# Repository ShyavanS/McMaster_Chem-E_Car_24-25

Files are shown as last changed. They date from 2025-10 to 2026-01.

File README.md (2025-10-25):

# McMaster_Chem-E_Car_24-25
The codebase for the McMaster Chem-E Car Team from 2024-2025.

This project uses an Adafruit Feather RP2040 Adalogger microcontroller programmed in the Arduino programming language. The car runs off a chemical reaction and is stopped by a chemical reaction as well. However, the code and the microcontroller are used to start the stopping reaction and stir the mixtures while monitoring it to identify when to stop based on a temperature threshold. It also uses an IMU to keep the car going straight, a servo for starting the stopping reaction, two motor drivers to run the drive motors, and two motors for stirring the reactions. The car's main drive system will be powered from a custom-built alkaline battery while the remaining auxiliary systems are powered from a smaller Li-Po battery.

The major components used are as follows:<br />
2 - N20 100 RPM Motors (for drive system)<br />
2 - N20 1000 RPM Motor (for reaction stirring mechanisms)<br />
4 - SER0039 Servo Motor (for initially mixing reactants & steering)<br />
2 - DRV8847 Motor Drivers (only used as switches as per regulations)<br />
2 - AMT102 Rotary Encoders (for datalogging to tune braking model only)<br />
1 - DS18B20 Temperature Sensor (for measuring temperature of braking reaction)<br />
1 - Adafruit 9-DOF Orientation IMU Fusion Breakout (BNO085 for logging/maintaining heading)<br /> 
1 - Adafruit Feather RP2040 Adalogger Microcontroller<br />
1 - 5000 mAh Li-Po Battery<br />

This repository also contains the custom-made PCB design for the component wiring we are using this year. The design was made using Altium, source files & gerber files are present in this repository.

The main objective of the competition is to design a small car to carry a certain amount of weight a set distance while powering and stopping the vehicle with a chemical reaction. The distance and weight vary each year. The compectition is hosted by the American Institute of Chemical Engineers (AIChE).

Makes use of [pimoroni's encoder-pio driver](https://github.com/pimoroni/pimoroni-pico/tree/encoder-pio/drivers/encoder-pio) to count encoder ticks on the PIOs of the RP2040 to prefvent lost ticks due to higher priority interrupts and increase accuracy while decreasing CPU load. Minor modifications were made to remove debouncing functionality & delays.

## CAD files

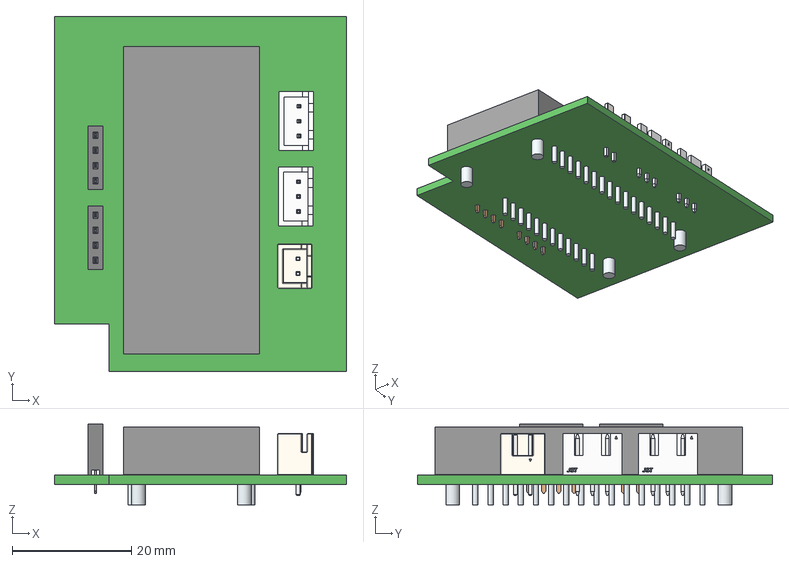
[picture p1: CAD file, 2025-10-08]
Car_Circuitry/Steering_Daughterboard.step
49.0 x 59.6 x 13.5 mm
Leads x 32
Pins x 2
Marking x 2
JST Logo x 2
B2B-XH-A
JST Logo adjustable
6130xx11821_PIN x 8

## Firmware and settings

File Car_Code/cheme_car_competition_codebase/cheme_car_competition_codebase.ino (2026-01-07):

// McMaster Chem-E Car Team
// Chem-E Car Competition Code - 24/25

/*
The code to be used at the Chem-E Car competition to run the car. Makes use of
an RP2040 microcontroller to drive the car and stop at a specified distance.
More information is available in the readme.
*/

// Included libraries
#include <OneWire.h>
#include <Adafruit_BNO08x.h>
#include <DallasTemperature.h>
#include <Servo.h>
#include <Adafruit_NeoPixel.h>
#include "hardware/timer.h"

#define NUM_LEDS 1 // Status LED

// Define drive motor pins
#define LEFT_PWM_1 9
#define LEFT_PWM_2 10
#define RIGHT_PWM_1 12
#define RIGHT_PWM_2 11

// Define the PWM pins for the stir bar motors
#define BRAK_STIR_PWM_1 A3
#define BRAK_STIR_PWM_2 24
#define PROP_STIR_PWM_1 6
#define PROP_STIR_PWM_2 5

// Define servo pins
#define BRAK_SERVO_PWM 13
#define PROP_SERVO_PWM 4
#define LEFT_SERVO_PWM MOSI
#define RIGHT_SERVO_PWM SCK

#define BRAK_TEMP_SENS A1 // Pin for the teperature sensor data line

#define BNO08X_RESET -1 // No reset pin for IMU over I2C, only enabled for SPI

// Struct for Euler Angles
struct euler_t
{
  float yaw;
  float pitch;
  float roll;
} ypr;

// Create servo objects
Servo brak_servo;
Servo prop_servo;
Servo left_servo;
Servo right_servo;

// Create BNO085 instance
Adafruit_BNO08x bno08x(BNO08X_RESET);
sh2_SensorValue_t sensor_value;

OneWire one_wire(BRAK_TEMP_SENS);          // Create a OneWire instance to communicate with the sensor
DallasTemperature temp_sensors(&one_wire); // Pass OneWire reference to Dallas Temperature sensor

Adafruit_NeoPixel pixel(NUM_LEDS, PIN_NEOPIXEL, NEO_GRB + NEO_KHZ800); // Status LED

// The target yaw angle to keep car straight
const float GOAL_YAW = 0.0;

// Rejection threshold for noise in IMU measurements
const float REJECT_THRESHOLD = 3.0;

// Define IMU variables
double raw_yaw;        // raw yaw angle
double prev_yaw;       // previous unwrapped yaw angle
double yaw;            // unwrapped yaw angle
double init_yaw = 0.0; // initial yaw angle
double yaw_diff = 0.0; // yaw angle difference

// Delta temperature
double temp_diff;

// Temperature change threshold
double temp_change;

// Last temperature fetched flag
bool last_fetch;

// variables to store temperature
double temperature_c; // Current temperature
double init_temp;     // Initial temperature for differential calculation

// KALMAN FILTER variables
double x_temp; // Filtered temperature
double p_temp; // Initial error covariance
double x_imu;  // Filtered temperature
double p_imu;  // Initial error covariance

// Process noise and measurement noise
double q_temp; // Process noise covariance
double r_temp; // Measurement noise covariance
double q_imu;  // Process noise covariance
double r_imu;  // Measurement noise covariance

// Keeping track of time
double curr_time = 0.0f;
double prev_time = 0.0f;
uint32_t start_time;

// PID loop variables
double error = 0.0;      // Proportional error
double last_error = 0.0; // Derivative error
double sum_error = 0.0;  // Integral error

// The following numbers need to be adjusted through testing
const float K_P = 13.0; // Proportional weighting
const float K_I = 0.0;  // Integral weighting
const float K_D = 0.0;  // Derivative weighting

// Offsets & constants for PID
int left_offset = 0;
int right_offset = 0;
const int SERVO_ANGLE = 1475;
const int MAX_OFFSET = 1024;
const int YAW_REF = 90;

/*
Description: Subroutine to drive car forward.
Inputs:      void
Outputs:     void
Parameters:  void
Returns:     void
*/
void drive_forward(void)
{
  digitalWrite(LEFT_PWM_1, HIGH);
  digitalWrite(RIGHT_PWM_2, HIGH);
  digitalWrite(LEFT_PWM_2, LOW);
  digitalWrite(RIGHT_PWM_1, LOW);
}

/*
Description: Subroutine to stop car and brake motors.
Inputs:      void
Outputs:     void
Parameters:  void
Returns:     void
*/
void stop_driving(void)
{
  digitalWrite(LEFT_PWM_1, HIGH);
  digitalWrite(RIGHT_PWM_2, HIGH);
  digitalWrite(LEFT_PWM_2, HIGH);
  digitalWrite(RIGHT_PWM_1, HIGH);
}

/*
Description: Subroutine to dump reactants into vessel.
Inputs:      void
Outputs:     void
Parameters:  (Servo)servo, (int)angle_us, (int)delay_ms
Returns:     void
*/
void servo_dump(Servo servo, int angle_us, int delay_ms)
{
  // Rotate to specified position
  servo.writeMicroseconds(angle_us);
  busy_wait_ms(500);
  servo.writeMicroseconds(angle_us);

  busy_wait_ms(delay_ms); // Wait specified delay

  // Return to default position
  servo.writeMicroseconds(450);
  busy_wait_ms(500);
  servo.writeMicroseconds(450);
}

/*
Description: Subroutine to set speed for reaction stir motors.
Inputs:      void
Outputs:     void
Parameters:  (int)stir_pin_1, (int)stir_pin_2, (int)speed
Returns:     void
*/
void start_stir(int stir_pin_1, int stir_pin_2, int speed) // Start stirring mechanism
{
  digitalWrite(stir_pin_1, LOW);  // For fast decay
  analogWrite(stir_pin_2, speed); // Set motor to speed obtained through testing
}

/*
Description: Subroutine to implement Kalman filtering on temperature sensor data.
Inputs:      void
Outputs:     (double)x_temp, (double)p_temp
Parameters:  (double)x_k, (double)p_k, (double)q, (double)r, (double)input
Returns:     void
*/
void kalman_filter(double x_k, double p_k, double q, double r, double input, bool tempTrue)
{
  // Kalman filter prediction
  double x_k_minus = x_k;     // Predicted next state estimate
  double p_k_minus = p_k + q; // Predicted error covariance for the next state

  // Kalman filter update

  /* Kalman gain: calculated based on the predicted error covariance
  and the measurement noise covariance, used to update the
  state estimate (x_k) and error covariance (p_k) */
  double k = p_k_minus / (p_k_minus + r); // Kalman gain

  // Comparison with actual sensor reading
  x_k = x_k_minus + k * (input - x_k_minus); // Updated state estimate
  p_k = (1 - k) * p_k_minus;                 // Updated error covariance

  if (tempTrue) // Update state for temperature sensor or IMU accordingly
  {
    x_temp = x_k;
    p_temp = p_k;
  }
  else
  {
    x_imu = x_k;
    p_imu = p_k;
  }
}

/*
Description: Subroutine to set the desired reports on the IMU.
Inputs:      void
Outputs:     void
Parameters:  void
Returns:     void
*/
void set_reports(void)
{
  if (!bno08x.enableReport(SH2_ROTATION_VECTOR))
  {
    exit(0);
  }
}

/*
Description: Subroutine convert quaternions from the IMU into euler angles to obtain yaw.
Inputs:      void
Outputs:     void
Parameters:  (float)qr, (float)qi, (float)qj, (float)qk, (euler_t)*ypr, (bool)degrees
Returns:     void
*/
void quaternion_to_euler(float qr, float qi, float qj, float qk, euler_t *ypr, bool degrees = false)
{
  float sqr = sq(qr);
  float sqi = sq(qi);
  float sqj = sq(qj);
  float sqk = sq(qk);

  ypr->yaw = atan2(2.0 * (qi * qj + qk * qr), (sqi - sqj - sqk + sqr));
  ypr->pitch = asin(-2.0 * (qi * qk - qj * qr) / (sqi + sqj + sqk + sqr));
  ypr->roll = atan2(2.0 * (qj * qk + qi * qr), (-sqi - sqj + sqk + sqr));

  if (degrees)
  {
    ypr->yaw *= RAD_TO_DEG;
    ypr->pitch *= RAD_TO_DEG;
    ypr->roll *= RAD_TO_DEG;
  }
}

/*
Description: Pointer subroutine for euler angles.
Inputs:      void
Outputs:     void
Parameters:  (sh2_RotationVectorWAcc_t)*rotational_vector, (float)qi, (euler_t)*ypr, (bool)degrees
Returns:     void
*/
void quaternion_to_euler_RV(sh2_RotationVectorWAcc_t *rotational_vector, euler_t *ypr, bool degrees = false)
{
  quaternion_to_euler(rotational_vector->real, rotational_vector->i, rotational_vector->j, rotational_vector->k, ypr, degrees);
}

/*
Description: PID loop subroutine to adjust steering angle.
Inputs:      (double)error, (double)sum_error, (double)last_error, (double)curr_time, (double)prev_time
Outputs:     (int)adj_pid_output
Parameters:  void
Returns:     void
*/
void pid_loop(void)
{
  // Generate output of controller based on constants & errors
  double pid_output = (error * K_P + sum_error * K_I + (error - last_error) / (curr_time - prev_time) * K_D) / YAW_REF * MAX_OFFSET;
  int adj_pid_output = max(min(round(pid_output), MAX_OFFSET), -MAX_OFFSET); // Clamp output to bounds

  // Get IMU reading to update error values
  bno08x.getSensorEvent(&sensor_value);
  quaternion_to_euler_RV(&sensor_value.un.rotationVector, &ypr, true);

  // Process yaw angle
  raw_yaw = ypr.yaw;
  unwrap_yaw();
  yaw_diff = yaw - init_yaw;

  kalman_filter(x_imu, p_imu, q_imu, r_imu, yaw_diff, false); // Kalman filtering for IMU data

  // Update errors
  last_error = error;
  error = GOAL_YAW - x_imu;
  sum_error = max(min(sum_error + cbrt(error), MAX_OFFSET), -MAX_OFFSET);

  // Write to servos
  left_servo.writeMicroseconds(SERVO_ANGLE - adj_pid_output);
  right_servo.writeMicroseconds(SERVO_ANGLE - adj_pid_output);
}

/*
Description: Subroutine to fetch temperature form the temperature sensor when the data is ready.
Inputs:      void
Outputs:     (double)temperature_c
Parameters:  void
Returns:     void
*/
void fetch_temp(void)
{
  temperature_c = temp_sensors.getTempCByIndex(0); // Get temperature in Celsius

  // Update temperature kalman filter
  kalman_filter(x_temp, p_temp, q_temp, r_temp, temperature_c, true);

  temp_diff = x_temp - init_temp; // Update delta temperature
  last_fetch = true;              // Raise fetch flag to signal ready
}

/*
Description: Subroutine to unwrap yaw angle to prevent discontinuities in the function over time.
Inputs:      (double)raw_yaw, (double)prev_yaw
Outputs:     (double)yaw
Parameters:  void
Returns:     void
*/
void unwrap_yaw(void)
{
  double delta = raw_yaw - prev_yaw;

  delta = fmod(delta + 180.0, 360.0);

  if (delta < 0.0)
  {
    delta += 360.0;
  }

  delta -= 180.0;

  // Reject any sudden noisy spikes
  if (fabs(delta) > REJECT_THRESHOLD)
  {
    yaw = prev_yaw;
    prev_yaw = yaw;
  }
  else
  {
    yaw = prev_yaw + delta;
    prev_yaw = yaw;
  }
}

/*
Description: Arduino setup subroutine.
Inputs:      void
Outputs:     void
Parameters:  void
Returns:     void
*/
void setup(void)
{
  // Indicate status to be initialized
  pixel.begin();
  pixel.setBrightness(255);
  pixel.show();
  pixel.setPixelColor(0, 255, 0, 0);
  pixel.show();

  // Setting to drive motors output mode
  pinMode(LEFT_PWM_1, OUTPUT);
  pinMode(LEFT_PWM_2, OUTPUT);
  pinMode(RIGHT_PWM_1, OUTPUT);
  pinMode(RIGHT_PWM_2, OUTPUT);

  stop_driving(); // Stop driving motors from any residual bootloader code

  // Initialize the stir motor pins as outputs
  pinMode(BRAK_STIR_PWM_1, OUTPUT);
  pinMode(BRAK_STIR_PWM_2, OUTPUT);
  pinMode(PROP_STIR_PWM_1, OUTPUT);
  pinMode(PROP_STIR_PWM_2, OUTPUT);

  // Setting the stir speed
  start_stir(BRAK_STIR_PWM_1, BRAK_STIR_PWM_2, 255);
  start_stir(PROP_STIR_PWM_1, PROP_STIR_PWM_2, 255);

  temp_sensors.begin();                     // Initialize the DS18B20 sensor
  temp_sensors.setResolution(11);           // Reduce resolution for faster polling
  temp_sensors.requestTemperatures();       // Request temperature from all devices on the bus
  temp_sensors.setWaitForConversion(false); // Disable blocking to allow multitasking

  init_temp = temp_sensors.getTempCByIndex(0); // Get temperature in Celsius
  temperature_c = init_temp;                   // Initialize temperature variable
  last_fetch = true;                           // Raise fetch flag to signal ready
  temp_diff = 0.0;                             // Initialize delta temperature to zero

  bno08x.begin_I2C();
  set_reports();

  // Poll IMU a few times & wait for initialization value to stabilize
  for (int i = 0; i < 5; i++)
  {
    bno08x.getSensorEvent(&sensor_value);
    quaternion_to_euler_RV(&sensor_value.un.rotationVector, &ypr, true);

    init_yaw = ypr.yaw;
    raw_yaw = init_yaw;
    prev_yaw = init_yaw;
    yaw = init_yaw;
    yaw_diff = yaw - init_yaw;

    busy_wait_ms(200);
  }

  // Initialize Kalman filter parameters
  x_temp = init_temp; // Initial state estimate
  p_temp = 0.1;       // Initial error covariance
  q_temp = 0.01;      // Process noise covariance
  r_temp = 0.5;       // Measurement noise covariance
  x_imu = yaw_diff;   // Initial state estimate
  p_imu = 0.007;      // Initial error covariance
  q_imu = 0.005;      // Process noise covariance
  r_imu = 0.01;       // Measurement noise covariance

  // Initialize servos to default position
  prop_servo.writeMicroseconds(450);
  prop_servo.attach(PROP_SERVO_PWM, 400, 2600);
  prop_servo.writeMicroseconds(450);
  busy_wait_ms(2000);
  brak_servo.writeMicroseconds(450);
  brak_servo.attach(BRAK_SERVO_PWM, 400, 2600);
  brak_servo.writeMicroseconds(450);
  busy_wait_ms(2000);
  left_servo.writeMicroseconds(1475);
  left_servo.attach(LEFT_SERVO_PWM, 400, 2600);
  left_servo.writeMicroseconds(1475);
  busy_wait_ms(2000);
  right_servo.writeMicroseconds(1475);
  right_servo.attach(RIGHT_SERVO_PWM, 400, 2600);
  right_servo.writeMicroseconds(1475);
  busy_wait_ms(2000);

  // Dump reactants before starting drive
  servo_dump(prop_servo, 2500, 3000);
  busy_wait_ms(7000);
  servo_dump(brak_servo, 2500, 3000);

  start_time = micros(); // First measurement saved seperately

  busy_wait_ms(17000);

  // Poll IMU one last time
  bno08x.getSensorEvent(&sensor_value);
  quaternion_to_euler_RV(&sensor_value.un.rotationVector, &ypr, true);

  init_yaw = ypr.yaw;
  raw_yaw = init_yaw;
  prev_yaw = init_yaw;
  yaw = init_yaw;
  yaw_diff = yaw - init_yaw;

  curr_time = (time_us_32() - start_time) / 1000000.0f; // Taken to update prev_time

  pixel.setPixelColor(0, 0, 0, 255); // Indicate setup complete status
  pixel.show();
}

/*
Description: Arduino loop subroutine.
Inputs:      void
Outputs:     void
Parameters:  void
Returns:     void
*/
void loop(void)
{
  drive_forward(); // Start drive

  prev_time = curr_time;

  // Only poll if flag indicates ready state
  if (last_fetch)
  {
    temp_sensors.requestTemperatures(); // Request temperature from all devices on the bus

    last_fetch = false; // System is no longer ready, lower flag
  }
  else if (temp_sensors.isConversionComplete())
  {
    fetch_temp(); // Fetch temperature after conversion, otherwise continue loop
  }

  curr_time = (time_us_32() - start_time) / 1000000.0f; // Taken to check time against first measurement

  pid_loop(); // Run PID controller

  temp_change = 0.185f * curr_time - 4.5f; // Calculate temperature change

  if (temp_diff <= temp_change)
  {
    // Stop driving
    stop_driving();

    // Indicate status to be finished
    pixel.setPixelColor(0, 0, 255, 0);
    pixel.show();

    while (1)
      ; // Do nothing for remainder of uptime
  }
}

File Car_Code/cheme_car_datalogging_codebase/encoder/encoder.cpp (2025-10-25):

#include <math.h>
#include <float.h>
#include "hardware/irq.h"
#include "hardware/clocks.h"
#include "encoder.hpp"

#ifndef NO_QSTR
#include "encoder.pio.h"
#endif

#define LAST_STATE(state) ((state) & 0b0011)
#define CURR_STATE(state) (((state) & 0b1100) >> 2)

namespace encoder
{

  ////////////////////////////////////////////////////////////////////////////////////////////////////
  // STATICS
  ////////////////////////////////////////////////////////////////////////////////////////////////////
  Encoder *Encoder::encoders[][NUM_PIO_STATE_MACHINES] = {{nullptr, nullptr, nullptr, nullptr}, {nullptr, nullptr, nullptr, nullptr}};
  uint8_t Encoder::claimed_sms[] = {0x0, 0x0};
  uint Encoder::pio_program_offset[] = {0, 0};

  Encoder::Capture::Capture()
      : captured_count(0), captured_delta(0), captured_frequency(0.0f), counts_per_rev(INT32_MAX)
  {
  }

  Encoder::Capture::Capture(int32_t count, int32_t delta, float frequency, float counts_per_rev)
      : captured_count(count), captured_delta(delta), captured_frequency(frequency), counts_per_rev(MAX(counts_per_rev, FLT_EPSILON))
  { // Clamp counts_per_rev to avoid potential NaN
  }

  int32_t Encoder::Capture::count() const
  {
    return captured_count;
  }

  int32_t Encoder::Capture::delta() const
  {
    return captured_delta;
  }

  float Encoder::Capture::frequency() const
  {
    return captured_frequency;
  }

  float Encoder::Capture::revolutions() const
  {
    return (float)captured_count / counts_per_rev;
  }

  float Encoder::Capture::degrees() const
  {
    return revolutions() * 360.0f;
  }

  float Encoder::Capture::radians() const
  {
    return revolutions() * M_TWOPI;
  }

  float Encoder::Capture::revolutions_delta() const
  {
    return (float)captured_delta / counts_per_rev;
  }

  float Encoder::Capture::degrees_delta() const
  {
    return revolutions_delta() * 360.0f;
  }

  float Encoder::Capture::radians_delta() const
  {
    return revolutions_delta() * M_TWOPI;
  }

  float Encoder::Capture::revolutions_per_second() const
  {
    return captured_frequency / counts_per_rev;
  }

  float Encoder::Capture::revolutions_per_minute() const
  {
    return revolutions_per_second() * 60.0f;
  }

  float Encoder::Capture::degrees_per_second() const
  {
    return revolutions_per_second() * 360.0f;
  }

  float Encoder::Capture::radians_per_second() const
  {
    return revolutions_per_second() * M_TWOPI;
  }

  Encoder::Encoder(PIO pio, uint sm, const pin_pair &pins, uint common_pin, Direction direction,
                   float counts_per_rev, bool count_microsteps, uint16_t freq_divider)
      : pio(pio), sm(sm), enc_pins(pins), enc_common_pin(common_pin), enc_direction(direction), enc_counts_per_rev(MAX(counts_per_rev, FLT_EPSILON)), count_microsteps(count_microsteps), freq_divider(freq_divider), clocks_per_time((float)(clock_get_hz(clk_sys) / (ENC_LOOP_CYCLES * freq_divider)))
  {
  }

  Encoder::~Encoder()
  {
    if (initialised)
    {
      pio_sm_set_enabled(pio, sm, false);
      pio_sm_unclaim(pio, sm);

      uint pio_idx = pio_get_index(pio);
      encoders[pio_idx][sm] = nullptr;
      claimed_sms[pio_idx] &= ~(1u << sm);

      hw_clear_bits(&pio->inte1, PIO_IRQ1_INTE_SM0_RXNEMPTY_BITS << sm);

      // If there are no more SMs using the encoder program, then we can remove it from the PIO
      if (claimed_sms[pio_idx] == 0)
      {
        pio_remove_program(pio, &encoder_program, pio_program_offset[pio_idx]);

        if (pio_idx == 0)
        {
          irq_remove_handler(PIO0_IRQ_1, pio0_interrupt_handler);
        }
        else
        {
          irq_remove_handler(PIO1_IRQ_1, pio1_interrupt_handler);
        }
      }

      // Reset all the pins this PWM will control back to an unused state
      gpio_set_function(enc_pins.a, GPIO_FUNC_NULL);
      gpio_set_function(enc_pins.b, GPIO_FUNC_NULL);

      if (enc_common_pin != PIN_UNUSED)
      {
        gpio_set_function(enc_common_pin, GPIO_FUNC_NULL);
      }
    }
  }

  void Encoder::pio_interrupt_handler(uint pio_idx)
  {
    // Go through each SM on the PIO to see which triggered this interrupt,
    // and if there's an associated encoder, have it update its state
    for (uint8_t sm = 0; sm < NUM_PIO_STATE_MACHINES; sm++)
    {
      if (encoders[pio_idx][sm] != nullptr)
      {
        encoders[pio_idx][sm]->process_steps();
      }
    }
  }

  void Encoder::pio0_interrupt_handler()
  {
    pio_interrupt_handler(0);
  }

  void Encoder::pio1_interrupt_handler()
  {
    pio_interrupt_handler(1);
  }

  bool Encoder::init()
  {
    if (!initialised && !pio_sm_is_claimed(pio, sm))
    {
      // Are the pins we want to use actually valid?
      if ((enc_pins.a < NUM_BANK0_GPIOS) && (enc_pins.b < NUM_BANK0_GPIOS))
      {

        // If a Pin C was defined, and valid, set it as a GND to pull the other two pins down
        if ((enc_common_pin != PIN_UNUSED) && (enc_common_pin < NUM_BANK0_GPIOS))
        {
          gpio_init(enc_common_pin);
          gpio_set_dir(enc_common_pin, GPIO_OUT);
          gpio_put(enc_common_pin, false);
        }

        pio_sm_claim(pio, sm);
        uint pio_idx = pio_get_index(pio);

        // If this is the first time using an encoder on this PIO, add the program to the PIO memory
        if (claimed_sms[pio_idx] == 0)
        {
          pio_program_offset[pio_idx] = pio_add_program(pio, &encoder_program);
        }

        // Initialise the A and B pins of this encoder
        pio_gpio_init(pio, enc_pins.a);
        pio_gpio_init(pio, enc_pins.b);
        gpio_pull_up(enc_pins.a);
        gpio_pull_up(enc_pins.b);

        // Set their default direction
        pio_sm_set_consecutive_pindirs(pio, sm, enc_pins.a, 1, false);
        pio_sm_set_consecutive_pindirs(pio, sm, enc_pins.b, 1, false);

        pio_sm_config c = encoder_program_get_default_config(pio_program_offset[pio_idx]);
        sm_config_set_jmp_pin(&c, enc_pins.a);
        sm_config_set_in_pins(&c, enc_pins.b);

        sm_config_set_in_shift(&c, false, false, 1);
        sm_config_set_fifo_join(&c, PIO_FIFO_JOIN_RX);

        sm_config_set_clkdiv_int_frac(&c, freq_divider, 0);

        pio_sm_init(pio, sm, pio_program_offset[pio_idx], &c);

        hw_set_bits(&pio->inte1, PIO_IRQ1_INTE_SM0_RXNEMPTY_BITS << sm);
        if (claimed_sms[pio_idx] == 0)
        {
          // Configure the processor to run pio_handler() when PIO IRQ 0 is asserted
          if (pio_idx == 0)
          {
            irq_add_shared_handler(PIO0_IRQ_1, pio0_interrupt_handler, PICO_SHARED_IRQ_HANDLER_DEFAULT_ORDER_PRIORITY);
            irq_set_enabled(PIO0_IRQ_1, true);
          }
          else
          {
            irq_add_shared_handler(PIO1_IRQ_1, pio1_interrupt_handler, PICO_SHARED_IRQ_HANDLER_DEFAULT_ORDER_PRIORITY);
            irq_set_enabled(PIO1_IRQ_1, true);
          }
        }
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

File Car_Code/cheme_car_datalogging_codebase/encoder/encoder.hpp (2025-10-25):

#pragma once

#include "hardware/pio.h"
#include "pimoroni_common.hpp"

using namespace pimoroni;

namespace encoder
{
  static constexpr float MMME_CPR = 12.0f;
  static constexpr float ROTARY_CPR = 24.0f;

  class Encoder
  {
    //--------------------------------------------------
    // Constants
    //--------------------------------------------------
  public:
    static constexpr float DEFAULT_COUNTS_PER_REV = ROTARY_CPR;
    static const bool DEFAULT_COUNT_MICROSTEPS = false;
    static const uint16_t DEFAULT_FREQ_DIVIDER = 1;

  private:
    static const uint32_t STATE_A_MASK = 0x80000000;
    static const uint32_t STATE_B_MASK = 0x40000000;
    static const uint32_t STATE_A_LAST_MASK = 0x20000000;
    static const uint32_t STATE_B_LAST_MASK = 0x10000000;

    static const uint32_t STATES_MASK = STATE_A_MASK | STATE_B_MASK |
                                        STATE_A_LAST_MASK | STATE_B_LAST_MASK;

    static const uint32_t TIME_MASK = 0x0fffffff;

    //--------------------------------------------------
    // Enums
    //--------------------------------------------------
  private:
    enum StepDir
    {
      NO_DIR = 0,
      INCREASING = 1,
      DECREASING = -1,
    };

    enum MicroStep : uint8_t
    {
      MICROSTEP_0 = 0b00,
      MICROSTEP_1 = 0b10,
      MICROSTEP_2 = 0b11,
      MICROSTEP_3 = 0b01,
    };

    //--------------------------------------------------
    // Substructures
    //--------------------------------------------------
  public:
    class Capture
    {
      //--------------------------------------------------
      // Variables
      //--------------------------------------------------
    private:
      int32_t captured_count;
      int32_t captured_delta;
      float captured_frequency;
      float counts_per_rev;

      //--------------------------------------------------
      // Constructors
      //--------------------------------------------------
    public:
      Capture();
      Capture(int32_t count, int32_t delta, float frequency, float counts_per_rev);

      //--------------------------------------------------
      // Methods
      //--------------------------------------------------
    public:
      int32_t count() const;
      int32_t delta() const;
      float frequency() const;

      float revolutions() const;
      float degrees() const;
      float radians() const;

      float revolutions_delta() const;
      float degrees_delta() const;
      float radians_delta() const;

      float revolutions_per_second() const;
      float revolutions_per_minute() const;
      float degrees_per_second() const;
      float radians_per_second() const;
    };

    //--------------------------------------------------
    // Variables
    //--------------------------------------------------
  private:
    PIO pio;
    uint sm;
    pin_pair enc_pins;
    uint enc_common_pin;
    Direction enc_direction;
    float enc_counts_per_rev;

    const bool count_microsteps;
    const uint16_t freq_divider;
    const float clocks_per_time;

    //--------------------------------------------------

    volatile bool enc_state_a = false;
    volatile bool enc_state_b = false;
    volatile int32_t enc_count = 0;
    volatile int32_t enc_cumulative_time = 0;
    volatile int16_t enc_step = 0;
    volatile int16_t enc_turn = 0;

    volatile int32_t microstep_time = 0;
    volatile StepDir step_dir = NO_DIR;

    int32_t last_count = 0;
    int32_t last_capture_count = 0;

    bool initialised = false;

    //--------------------------------------------------
    // Statics
    //--------------------------------------------------
    static Encoder *encoders[NUM_PIOS][NUM_PIO_STATE_MACHINES];
    static uint8_t claimed_sms[NUM_PIOS];
    static uint pio_program_offset[NUM_PIOS];
    static void pio_interrupt_handler(uint pio_idx);
    static void pio0_interrupt_handler();
    static void pio1_interrupt_handler();

    //--------------------------------------------------
    // Constructors/Destructor
    //--------------------------------------------------
  public:
    Encoder(PIO pio, uint sm, const pin_pair &pins, uint common_pin = PIN_UNUSED, Direction direction = NORMAL_DIR,
            float counts_per_rev = DEFAULT_COUNTS_PER_REV, bool count_microsteps = DEFAULT_COUNT_MICROSTEPS,
            uint16_t freq_divider = DEFAULT_FREQ_DIVIDER);
    ~Encoder();

    //--------------------------------------------------
    // Methods
    //--------------------------------------------------
  public:
    bool init();

    // For print access in micropython
    pin_pair pins() const;
    uint common_pin() const;

    bool_pair state() const;
    int32_t count() const;
    int32_t delta();
    void zero();

    int16_t step() const;
    int16_t turn() const;

    float revolutions() const;
    float degrees() const;
    float radians() const;

    //--------------------------------------------------

    Direction direction() const;
    void direction(Direction direction);

    float counts_per_rev() const;
    void counts_per_rev(float counts_per_rev);

    Capture capture();

    //--------------------------------------------------
  private:
    void process_steps();
    void microstep(int32_t time_since, bool up);
  };

}

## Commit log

2024-11-20 Added Small Text
    [Car_Circuitry.SchDoc]
2024-11-27 remove old IMU
    [Car_Circuitry.PcbDoc, Car_Circuitry.SchDoc]
2025-01-08 Implementing changes from comment
    initialized x_temp, and initialized x_k_temp as initTemp. updated ecvalue to use the filtered temp, and fixed the mistake in the calling of the temperature kalman filter function. Added the changes to the datalogging code base.
    [cheme_car_competition_codebase.ino, cheme_car_datalogging_codebase.ino]
2025-01-12 Fix Issues
    Got rid of x_temp, gave initial values to Kalman variables in the setup loop rather than at the top.
    [cheme_car_competition_codebase.ino, cheme_car_datalogging_codebase.ino]
2025-01-19 Reverse Polarity Protection
    Added a schottky diode for reverse polarity protection for the battery.
    [Car_Circuitry.PcbDoc, Car_Circuitry.PrjPcb, Car_Circuitry.SchDoc]
2025-02-12 Remove conductivity sensor and added buck boost converter interrupt.
    Removed code that is related to the conductivity sensor. Added code for an interrupt for the buck boost converter for short circuit/ overcurrent/ overvoltage
    [cheme_car_competition_codebase.ino, cheme_car_datalogging_codebase.ino]
2025-02-22 Fixing Issues
    Removed buck boost converter stuff from the competition codebase. Fixed the small issues in the datalogging codebase.
    [cheme_car_competition_codebase.ino, cheme_car_datalogging_codebase.ino]
2025-03-06 changes for manual pid controller
2025-09-30 maybe pid works? datalogging is current, comp is not.
2025-09-30 working PID, mechanical needs changes
2025-10-01 updated comp & caught some bugs
    [cheme_car_competition_codebase.ino, cheme_car_datalogging_codebase.ino]
2025-10-01 unwrapped angles & fixed integral
    [cheme_car_competition_codebase.ino, cheme_car_datalogging_codebase.ino]
2025-10-08 crude, but might work, assume any measurement with too high a slew rate is noise and use last reliable measurement instead.
    [Steering_Daughterboard.step]
2025-10-25 update readme, switched from interrupts to PIO for encoder logging, updated wheel circumference, hardware timers, removed all sources of error in datalogging so car stops on a dime from a solely mech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
    [cheme_car_competition_codebase.ino, cheme_car_datalogging_codebase.ino, encoder.cpp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]
